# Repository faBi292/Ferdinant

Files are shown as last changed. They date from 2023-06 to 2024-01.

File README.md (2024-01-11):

# Ferdinant©️

---

## **IDLE Screens**

Es gibt 4 Anzeigen die mit den A,B,C und D ausgewählt werden können.

### **IDLE A**

<pre><code>Uhrzeit: hh:mm:ss
Tag: XX   LH:hh,h
</code></pre>

- "Uhrzeit", zeigt die interne Uhrzeit der Steuerung.
- "Tag", zeigt den aktuellen Tag des Modi, startet bei Tag 1.
- "LH", steht für Light Hours und gibt an wie viele Stunden Licht an diesem Tag schon vergangen sind.

### **IDLE B**

<pre><code>Rising: hh:mm:ss
Dawn  : hh:mm:ss
</code></pre>

- "Rising", gibt an wann das nächste mal das Licht angeschaltet wird.
- "Dawn", gibt an wann das Licht das nächste mal ausgeschaltet wird.

### **IDLE C**

<pre><code>Cycle: "MODE"
"MODE NAME"   "Days"
</code></pre>

- "MODE", gibt an welcher Modus gerade aktiv ist. (2002, 2004, 2006)
- "Mode Name", gibt den Namen des aktuellen Modus zurück (Half_Season, Full_season, Tropical)
- "Days", gibt an wie viele Tage der Modi benötigt.

### **IDLE D**

<pre><code>Glow: "%"

</code></pre>

- "Glow", gibt an wie groß die Lichtintensität des Lichtsensor ist.
- ℹ️ Das Licht gilt als an bei über 80% und als aus bei 30%, dazwischen ist eine Grauzone/Puffer und wechselt erst wenn die Schwelle über/unterschritten wurde.

---

## **LED's**

| Farbe | Bedeutung |
| --- | --- |
| 🔵 Blau | Leuchtet wenn Steckdose "An" sein soll und ist aus wenn Steckdose "Aus" sein soll. |
| 🟡 Gelb | Leuchtet auf wenn gefunkt wird. |
| 🔴 Rot  | Leuchtet wenn Fehler erkannt wird, unzwar wenn Lichtsensor nicht mit dem internen Wert übereinstimmt. |

---

## **Modus Auswahl**

Da zwischen 3 Modis unterschieden werden muss, ist wichtig zu verstehen wie man den Modi richtig einstellt.

Nach dreimaligen druecken der Sternchen Taste   `"*"`  auf dem Keypad, fragt das System, ob es einen Reset durch fuehren soll. Welches mit `"#"` bestaetigt werden kann, mit dem Druck einer anderen Taste wird das Menue automatischen wieder verlassen.

<pre><code>RESET MENU!
USE '#' 4 RESE
</code></pre>

Beachte, dass es moeglich ist zu jedem Zeitpunkt des Resetsablaufes, dass System kurz vom auszuschalten um den Vorgang zu unterbrechen. Dadurch wird einfach der Zustand vor dem Modi Auswahl beibehalten.

⚠️ Beachtet werden muss, dass während man in der Auswahl ist, dass System nicht die Steckdose steuern kann.

### **Jahr einstellen**

Wird der Reset bestaetigt oeffnet sich, das Menue das fragt welcher Modi ausgewaehlt werden soll. Dazu muss ein 4-stelliger Code eingegebn werden.Es tritt ein Fehler auf, wenn ein Code eingegben wird den das System nicht kennt. Danach wird man erneut angewiesen einen Code einzugeben.

**Dynamische Zyklen**

| Modi-Code | Modi-Name | Dauer |
| --- | --- | --- |
| 2000 | Half Season | 80 Tage  |
| 2001 | Full Season | 120 Tage |
| 2002 | Tropical | 100 Tage |

**Statische Zyklen**

| Modi-Code | Modi-Name | Lichtstunden pro Tag | Zeiten |
| --- | --- | --- | --- |
| 2003 | Veggie | 18h | 05:00 - 23:00 |
| 2004 | Production | 12h | 08:00 - 20:00 |
| 2005 | Short Veggie | 16h | 06:00 - 22:00 |

### **Setzen der Uhrzeit**

Ist der Code eingegebn wird nun nach der Uhrzeit (Stunde und Minute) gefragt. Hier empfielt es sich die aktuelle Uhrzeit zu benutzen um die Steuerung der Tageszeit anzupassen. Natuerlich ist eine andere Uhrzeit auch moeglich.
(Beachte: bei der Eingabe einer einstelligen Zahl wird folgende Formatierung erwartet Bsp.: fuer 6 Uhr muesste **'06'** eingegeben werden, das selbe gilt fuer die Minuten).

<pre><code>Stunde eingeben
Bsp. '13'
</code></pre>

### Setzen des Tages

Nun kann eingestellt werden wie viele, Tage übersprugnen werden sollen.

<pre><code>Tage skippen
Bsp. '023'
</code></pre>

Bsp. um am Tag 8 anzufangen muss die Zahl **'007'** eingegeben werden.

---

# **Schaltzyklen**

- ℹ️ Sobald ein **dynamischer** Zyklus über sein Ende hinaus verwendet wird, setzt er fortlaufend seine letzten Schaltzeiten ein.

**Statische Zyklen**

| Modi-Code | Modi-Name | Lichtstunden pro Tag | Zeiten |
| --- | --- | --- | --- |
| 2003 | Veggie | 18h | 05:00 - 23:00 |
| 2004 | Production | 12h | 08:00 - 20:00 |
| 2005 | Short Veggie | 16h | 06:00 - 22:00 |



---

# **Schaltplan**

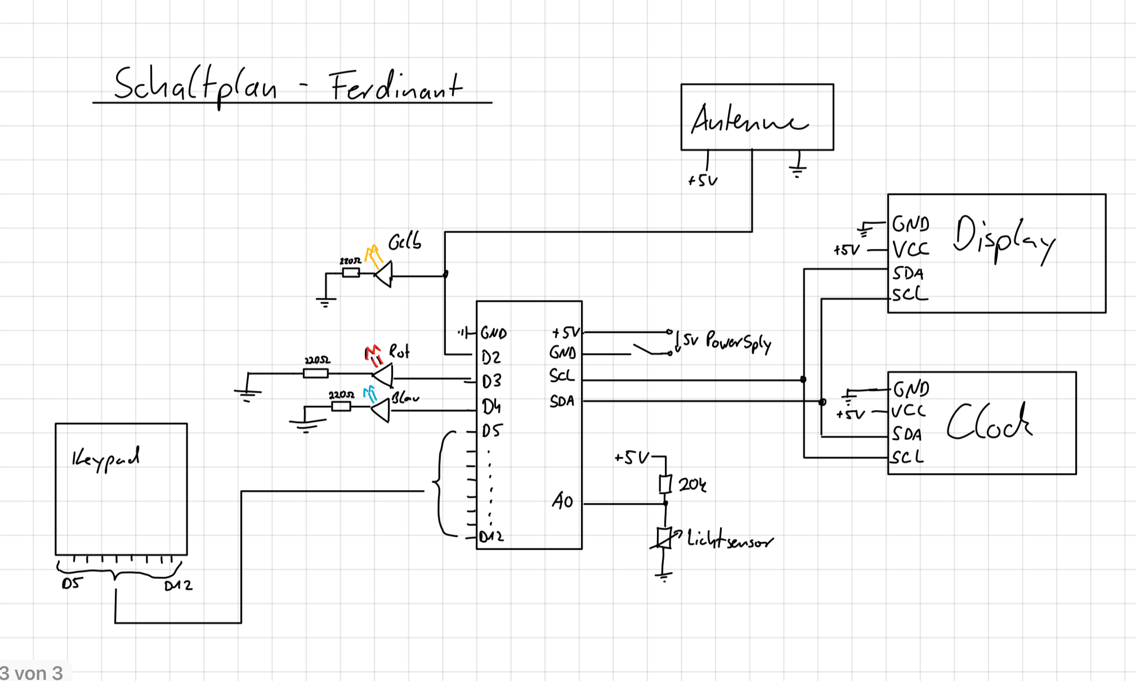
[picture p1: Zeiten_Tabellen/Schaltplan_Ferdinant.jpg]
Schaltplan


# **Code spezifische Notizen**

**Tri-State Codes**

<pre><code>AN = mySwitch.sendTriState("00000FFF0F0F");
</code></pre>

<pre><code>AUS = mySwitch.sendTriState("00000FFF0FF0");
</code></pre>

# Bauteile

| Komponente | Modell/Bezeichnung |
| --- | --- |
| Steckdose  | RCS 1000 N Comfort (Mx. 1000 Watt) |
| Uhr | RTC_DS3231 |
| Sender | 433_MHz Transmitter |
| Board | 16Mhz NANO V 3,0 Atmega328 |
| Display | LCD1602 |
| Keypad | 4x4 Matrix Tastatur |

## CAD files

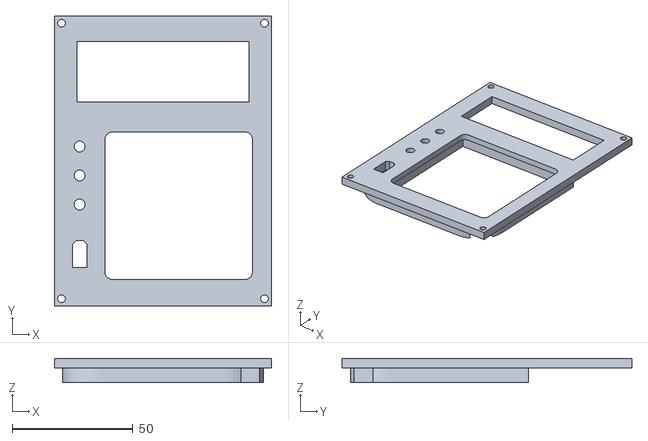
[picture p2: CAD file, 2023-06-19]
CAD_Modell/Ferdinant_Deckel_Sebi.stl
90.0 x 120.0 x 10.0

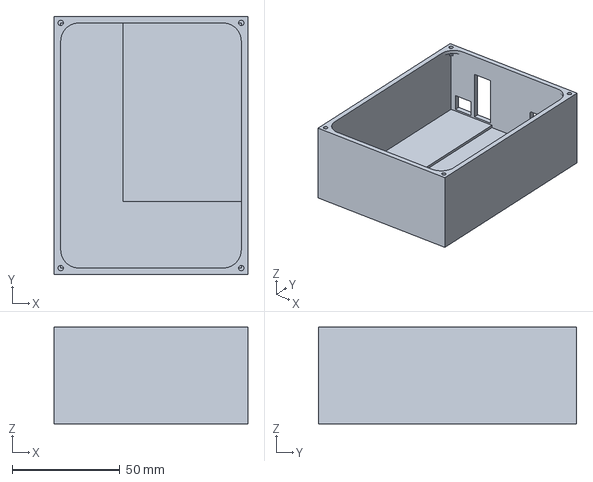
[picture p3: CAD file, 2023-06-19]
CAD_Modell/Ferdinant_Basis v2.3mf
90.0 x 120.0 x 45.0 mm

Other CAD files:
CAD_Modell/Ferdinant_Deckel_2.0 v2.3mf
CAD_Modell/Ferdinant_Basis_Sebi.stl
CAD_Modell/Ferdinant_Basis.stl
CAD_Modell/Ferdinant_Deckel.stl
CAD_Modell/Ferdinant_Basis v1.f3d
CAD_Modell/Ferdinant_Deckel v1.f3d

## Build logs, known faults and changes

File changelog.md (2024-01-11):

# CHANGELOG.md

## v1.3 (11.02.2024)

* 3 Neue Modi hinzugefügt (Veggie, Production, Short Veggie)

## v1.2 (01.05.2023)

- Offical Release

## v1.1-beta (01-05-2023)

- Modi's Angepasst 2002,2004,2006,
- I2C LCD Funktionen erweitert: ( Idle A,B,C und Energiespar Modus)
- Auf Nano Board umgestiegen
- Steckdose wird jetzt über Tri-State angestuert
- Implementierung des Lichtsensors

## v1.0-beta (26-03-2023)

- RC Modul funktionsfähig eingebunden
- Keypad Funktionen implementiert
- LCD Display integriert, 4 Idle-Modi, gute Ansteuerbarkeit der Knöpfe
- Reset Möglichkeit
- Bis jetzt nur ein Modi "2002"
- Kleine Test Led angebaut

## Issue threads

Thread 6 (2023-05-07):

im reset menu waitForKey() durch andere Loesung ersetzen um Sicherheit zu erhoehen

faBi292, 2023-05-07:

faBi292, 2023-10-01:
Es wurde in der readme auf das Problem hingewiesen und sollte leicht zu vermeiden sein.

Closed 2023-10-01.

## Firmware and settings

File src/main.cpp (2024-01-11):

#include <Arduino.h>
#include <Keypad.h>
#include <RTClib.h>
#include <SPI.h>
#include <Wire.h>
#include <LiquidCrystal_I2C.h>
#include <RCSwitch.h>

#define Red_LED_PIN 2
#define Blue_LED_PIN 3
#define RC_PIN 4

RTC_DS3231 rtc;
RCSwitch mySwitch;

const int HALF_SEASON = 2000;
const int FULL_SEASON = 2001;
const int TROPICAL = 2002;
const int VEGGIE = 2003;
const int PRODUCTION = 2004;
const int SHORT_VEGGIE = 2005;

const byte ROWS = 4; // four rows
const byte COLS = 4; // four columns

// Map the buttons to an array for the Keymap instance
char hexaKeys[ROWS][COLS] = {
    {'1', '2', '3', 'A'},
    {'4', '5', '6', 'B'},
    {'7', '8', '9', 'C'},
    {'*', '0', '#', 'D'}};

byte colPins[ROWS] = {5, 6, 7, 8};    // Pins used for the rows of the keypad
byte rowPins[COLS] = {9, 10, 11, 12}; // Pins used for the columns of the keypad

// Initialise the Keypad
Keypad customKeypad = Keypad(makeKeymap(hexaKeys), rowPins, colPins, ROWS, COLS);

typedef struct
{
  uint16_t jahr = 2008;
  uint8_t stunde = 13;
  uint8_t minute = 17;
  uint8_t sekunde = 8;
  uint16_t tag = 1;

} time_struct;

// const int rs = A0, en = A1, d4 = A2, d5 = A3, d6 = 10, d7 = 11;
// LiquidCrystal lcd(rs, en, d4, d5, d6, d7);
LiquidCrystal_I2C lcd(0x27, 16, 2); // I2C address, number of columns and rows

enum zustaende
{
  Knopf_A,
  Knopf_B,
  Knopf_C,
  Knopf_D,
};

int LICHT_CHECK_intern; // Sagt aus ob Licht an sein muss
int LICHT_CHECK_extern; // Sagt aus ob Licht gerade an ist via. Photosensor
unsigned days_passed;   // Vergangene Tage beginnend bei 1
char getKey_puffer;     // zuletzt eingegebene Taste wird hier gespeichert

void set_usertime();                                            // Erm├╢glicht den Benutzer seine Einstellung vorzunehmen.
void print_time();                                              // Printed die aktuelle Uhrzeit der Uhr
void print_time_passed();                                       // Printed die verstrichene Zeit seit anfang der Einstellung.
unsigned int get_days_passed();                                 // Berechnet die verstrichenen Tage seit anfang der Einstellung.
uint32_t get_seconds_passed_daily();                            // Berechnet die verstrichenen Sekunden seit 0 Uhr.
int check_status(uint32_t aufgang_sek, uint32_t untergang_sek); // gibt 1 f├╝r Licht muss an sein und 0 f├╝r Licht muss aus sein.
uint32_t get_offset();                                          // Berechnet den Offset in bezug zu 1970 zu dem jeweiligen start datum der einstellung. Bsp sekunden von 1970 bis 2002
void increaseDateTime(DateTime &dt, int days);                  // Erh├╢ht das Datum einer DateTime Variablen um eine Anzahl von Tagen
void check_star();                                              // ├£berpr├╝ft ob die Sternchentaste gedr├╝ckt geahlten wird, nach 3 Sekunden f├╝hrt sie dann set_usertime() aus.
uint32_t check_aufgang_sek(unsigned int days);                  // Bekommt die vergangen Tage ├╝bergeben und gibt die Aufgangsuhrzeit zur├╝ck
uint32_t check_untergang_sek(unsigned int days);                // Bekommt die vergangen Tage ├╝bergeben und gibt die Untergangsuhrzeit zur├╝ck
void display_idle(char Knopf);                                  // Bekommt A,B,C,D ├╝bergebn und wechselt dann in den entsprechenden Modi
void check_Knopf();                                             // ├£berpr├╝ft ob Knopf gedr├╝ckt wurde und ruft entsprechend die Funktion auf
void secondsToTime(uint32_t seconds, char *timeString);         // Bekommt Sekunden als eingabe Wert und gibt sie ahls "HH:MM" format aus
void secondsToFullTime(uint32_t seconds, char *timeString);     // Bekommt Sekunden als eingabe Wert und gibt sie ahls "HH:MM:SS" format aus
void secondsToHour(uint32_t seconds, char *timeString);         // Bekommt Sekunden als eingabe Wert und gibt sie ahls "HH,H" format aus
float read_LichtSensor();                                       // Gibt die Aktuelle Lichtintensität in % zurück
uint32_t get_lightseconds();                                    // Gibt die Sekunden die an dem Tag schon das Lich an ist wieder

void init_RCSwitch(int PIN, int PulseLength);
void steckdose_on(int state); // Kann Steckdose ein und ausschalten 1:EIN / 0:AUS

void lcd_energiesparen(int timer_reset); // Steuert die Hitnergrundbeleuchtung
int licht_check_photosensor();

// void transmit_data(int state);

void setup()
{
  Serial.begin(9600); // Initialise the serial monitor

  lcd.init();
  lcd_energiesparen(1);

  lcd.print("Loading");
  delay(300);
  lcd.print(".");
  delay(300);
  lcd.print(".");
  delay(300);
  lcd.print(".");
  delay(300);

  Wire.begin();
  rtc.begin();

  init_RCSwitch(RC_PIN, 324);

  if (!rtc.begin())
  {
    lcd.clear();
    lcd.println("RTC not found!");
    while (1)
      ;
  }

  pinMode(Red_LED_PIN, OUTPUT);  // Rote LED
  pinMode(Blue_LED_PIN, OUTPUT); // Blaue LED

  pinMode(A0, INPUT); // Licht_Sensor

  /*digitalWrite(Red_LED_PIN, HIGH);
  for (int i = 1; i < 121; i++)
  {
    Serial.println((String)i + ":" + check_aufgang_sek(i) + ":" + check_untergang_sek(i));
  }*/
  // DateTime dt1(2006, 1, 1, 0, 0, 0); //Findet den Offset raus
  // Serial.println(dt1.unixtime());
}

void loop()
{
  static unsigned long lastTime_1000 = 0;
  static unsigned long lastTime_30000 = 0;

  check_Knopf();

  if (millis() - lastTime_1000 >= 1000)
  {

    lastTime_1000 = millis(); // setzt Schleife zur├╝ck

    days_passed = get_days_passed();

    LICHT_CHECK_intern = check_status(check_aufgang_sek(days_passed), check_untergang_sek(days_passed)); // 6.5ms
    analogWrite(Blue_LED_PIN, LICHT_CHECK_intern * 30);
    LICHT_CHECK_extern = licht_check_photosensor();

    static boolean status = !LICHT_CHECK_intern; // Gibt an ob die Initialsendung nach Switch schon erfolgt ist
    if (status != LICHT_CHECK_intern)
    {
      status = LICHT_CHECK_intern;
      steckdose_on(LICHT_CHECK_intern);
    }

    if (LICHT_CHECK_extern != LICHT_CHECK_intern)
    {
      digitalWrite(Red_LED_PIN, HIGH);
      steckdose_on(LICHT_CHECK_intern);
    }
    else
    {
      digitalWrite(Red_LED_PIN, LOW);
    }

    lcd_energiesparen(0); // Aktualisiert die energiespar Funktion

    display_idle(' '); // 9ms
  }

  if (millis() - lastTime_30000 >= 30000) // Setzt alle 30 Sekunden Signal raus
  {
    lastTime_30000 = millis(); // setzt Schleife zur├╝ck

    if (LICHT_CHECK_intern)
    {
      steckdose_on(1);
    }
    else
    {
      steckdose_on(0);
    }
  }
}

void check_Knopf()
{
  getKey_puffer = customKeypad.getKey();

  if (getKey_puffer)
  {
    lcd_energiesparen(1);
  }
  if (getKey_puffer == 'A')
  {
    display_idle('A');
  }
  else if (getKey_puffer == 'B')
  {
    display_idle('B');
  }
  else if (getKey_puffer == 'C')
  {
    display_idle('C');
  }
  else if (getKey_puffer == 'D')
  {
    display_idle('D');
  }
  else if (getKey_puffer == '*')
  {
    check_star();
  }
  else if (getKey_puffer == '0')
  {
    steckdose_on(0);
  }
  else if (getKey_puffer == '1')
  {
    steckdose_on(1);
  }
}

void display_idle(char Knopf)
{
  static DateTime now;
  static zustaende idle_zustand = Knopf_A;
  static char puffer = Knopf_A;
  static char time_puffer[10];

  if (Knopf != ' ')
  {
    puffer = Knopf;
  }

  if (puffer == 'A')
  {
    idle_zustand = Knopf_A;
  }
  else if (puffer == 'B')
  {
    idle_zustand = Knopf_B;
  }
  else if (puffer == 'C')
  {
    idle_zustand = Knopf_C;
  }
  else if (puffer == 'D')
  {
    idle_zustand = Knopf_D;
  }

  switch (idle_zustand)
  {
  case Knopf_A:

    secondsToFullTime(get_seconds_passed_daily(), time_puffer);
    lcd.setCursor(0, 0);
    lcd.print((String) "Uhrzeit:" + time_puffer + "    ");
    lcd.setCursor(0, 1);
    lcd.print((String) "Tag:" + get_days_passed() + "   ");
    lcd.setCursor(8, 1);
    secondsToHour(get_lightseconds(), time_puffer);
    lcd.print((String) "LH:" + time_puffer + "h        ");
    break;

  case Knopf_B:

    secondsToFullTime(check_aufgang_sek(get_days_passed()), time_puffer);
    lcd.setCursor(0, 0);
    lcd.print((String) "Rising: " + time_puffer + "   ");
    secondsToFullTime(check_untergang_sek(get_days_passed()), time_puffer);
    lcd.setCursor(0, 1);
    lcd.print((String) "Dawn  : " + time_puffer + "   ");
    break;

  case Knopf_C:

    now = rtc.now();

    lcd.setCursor(0, 0);
    lcd.print((String) "Cycle: " + now.year() + "      ");
    lcd.setCursor(0, 1);
    if (now.year() == HALF_SEASON)
    {
      lcd.print("Half Season  80d  ");
    }
    else if (now.year() == FULL_SEASON)
    {
      lcd.print("Full Season 120d ");
    }
    else if (now.year() == TROPICAL)
    {
      lcd.print("Tropical    100d ");
    }
    else if (now.year() == VEGGIE)
    {
      lcd.print("Veggie       18h ");
    }
    else if (now.year() == PRODUCTION)
    {
      lcd.print("Production   12h ");
    }
    else if (now.year() == SHORT_VEGGIE)
    {
      lcd.print("Short Veg.   16h ");
    }
    else
    {
      lcd.print("NO MODE          ");
    }

    break;

  case Knopf_D:

    static float brightness_precent;

    brightness_precent = read_LichtSensor();

    lcd.setCursor(0, 0);
    lcd.print((String) "Glow: " + brightness_precent + "%           ");
    lcd.setCursor(0, 1);

    lcd.print((String) "                         ");

    break;
  }
}

void check_star()
{
  static uint8_t counter = 0;
  static unsigned long lasttime = 0;

  // Serial.println(millis() - lasttime);

  if (millis() - lasttime >= 1000)
  {
    counter = 0;
    lasttime = millis();
  }

  if (getKey_puffer == '*')
  {
    counter++;
    lasttime = millis();
  }

  if (counter > 2)
  {
    lcd.clear();
    lcd.setCursor(0, 0);
    lcd.print("RESET MENU!");
    lcd.setCursor(0, 1);
    lcd.print("USE '#' 4 RESET");

    if (customKeypad.waitForKey() == '#') // hier m∩┐╜sste eigentlich eine bessere L∩┐╜sung her
    {
      set_usertime();
      counter = 0;
    }
    else
    {
      counter = 0;
    }
  }
}

void set_usertime()
{
  int set_process = 0;   // Zaehler Variable
  time_struct user_time; // Defeniert neuen Zeit Speicher

  // erste Schleife f├╝r Jahr / Code
  do
  {
    lcd.clear();
    lcd.setCursor(0, 0);
    lcd.print("Modi eingeben");
    lcd.setCursor(0, 1);
    lcd.print("Bsp.'2008' ");

    char user_time_code[5] = "2008";

    for (int i = 0; i < 4; i++)
    {
      user_time_code[i] = customKeypad.waitForKey();
      lcd.print(user_time_code[i]);
    }
    delay(400);
    lcd.clear();
    lcd.print("Eingabe: ");
    lcd.print(user_time_code[0]);
    lcd.print(user_time_code[1]);
    lcd.print(user_time_code[2]);
    lcd.print(user_time_code[3]);
    // Serial.println(String("Eingabe: ") + user_time_code[0] + user_time_code[1] + user_time_code[2] + user_time_code[3]);

    if (atoi(user_time_code) == HALF_SEASON)
    {
      set_process = 1;
      user_time.jahr = atoi(user_time_code);
      lcd.setCursor(0, 1);
      lcd.print("HALF SEASON");
      delay(2000);
    }
    else if (atoi(user_time_code) == FULL_SEASON)
    {
      set_process = 1;
      user_time.jahr = atoi(user_time_code);
      lcd.setCursor(0, 1);
      lcd.print("FULL SEASON");
      delay(2000);
    }
    else if (atoi(user_time_code) == TROPICAL)
    {
      set_process = 1;
      user_time.jahr = atoi(user_time_code);
      lcd.setCursor(0, 1);
      lcd.print("TROPICAL");
      delay(2000);
    }
    else if (atoi(user_time_code) == VEGGIE)
    {
      set_process = 1;
      user_time.jahr = atoi(user_time_code);
      lcd.setCursor(0, 1);
      lcd.print("VEGGIE");
      delay(2000);
    }
    else if (atoi(user_time_code) == PRODUCTION)
    {
      set_process = 1;
      user_time.jahr = atoi(user_time_code);
      lcd.setCursor(0, 1);
      lcd.print("PRODUCTION");
      delay(2000);
    }
    else if (atoi(user_time_code) == SHORT_VEGGIE)
    {
      set_process = 1;
      user_time.jahr = atoi(user_time_code);
      lcd.setCursor(0, 1);
      lcd.print("SHORT_VEGGIE");
      delay(2000);
    }
    else
    {
      lcd.clear();
      lcd.print("NOT FOUND!");
      delay(600);
    }

  } while (set_process == 0);

  // zweite Schleife f├╝r Stunde
  do
  {
    lcd.clear();
    lcd.setCursor(0, 0);
    lcd.print("Stunde eingeben");
    lcd.setCursor(0, 1);
    lcd.print("Bsp.'13' ");

    char user_time_code[3] = "13";

    for (int i = 0; i < 2; i++)
    {
      user_time_code[i] = customKeypad.waitForKey();
      lcd.print(user_time_code[i]);
    }
    delay(400);
    lcd.clear();
    lcd.print("Eingabe: ");
    lcd.print(user_time_code[0]);
    lcd.print(user_time_code[1]);
    lcd.print(" Uhr!");
    delay(1000);

    if (atoi(user_time_code) < 24)
    {
      set_process = 2;
      user_time.stunde = atoi(user_time_code);
    }
    else
    {
      lcd.clear();
      lcd.print("UHRZEIT ZU GROSS");
      delay(600);
    }

  } while (set_process == 1);

  // dritte Schleife f├╝r Minuten
  do
  {
    lcd.clear();
    lcd.print("Minuten Eingeben");
    lcd.setCursor(0, 1);
    lcd.print("Bsp.'41' ");

    char user_time_code[3] = "41";

    for (int i = 0; i < 2; i++)
    {
      user_time_code[i] = customKeypad.waitForKey();
      lcd.print(user_time_code[i]);
    }

    delay(400);

    lcd.clear();
    lcd.print("Eingabe: ");
    lcd.print(user_time_code[0]);
    lcd.print(user_time_code[1]);
    lcd.print(" min!");

    delay(1000);

    if (atoi(user_time_code) < 60)
    {
      set_process = 3;
      user_time.minute = atoi(user_time_code);
    }
    else
    {
      lcd.clear();
      lcd.print("UHRZEIT ZU GROSS");
      delay(600);
    }

  } while (set_process == 2);

  // vierte Schleife f├╝r Tage
  do
  {
    lcd.clear();
    lcd.setCursor(0, 0);
    lcd.print("Tage skippen");
    lcd.setCursor(0, 1);
    lcd.print("Bsp.'023' ");

    char user_time_code[4] = "023";

    for (int i = 0; i < 3; i++)
    {
      user_time_code[i] = customKeypad.waitForKey();
      lcd.print(user_time_code[i]);
    }

    delay(400);
    lcd.clear();
    lcd.print("Eingabe: ");
    lcd.print(user_time_code[0]);
    lcd.print(user_time_code[1]);
    lcd.print(user_time_code[2]);
    delay(1000);

    if (atoi(user_time_code) < 300)
    {
      set_process = 4;

      rtc.adjust(DateTime(user_time.jahr, 1, 1, user_time.stunde, user_time.minute, 30) + TimeSpan(atoi(user_time_code), 0, 0, 0));
    }
    else
    {
      lcd.clear();
      lcd.println("TAGE ZU GROSS");
      delay(600);
    }

  } while (set_process == 3);

  lcd_energiesparen(1);
  lcd.clear();
  lcd.print("SUCCESS");
  lcd.setCursor(0, 1);
  lcd.print("Loading...");

  delay(2000);
}

void print_time()
{

  DateTime now = rtc.now();

  Serial.print(now.year(), DEC);
  Serial.print('/');
  Serial.print(now.month(), DEC);
  Serial.print('/');
  Serial.print(now.day(), DEC);
  Serial.print(' ');
  Serial.print(now.hour(), DEC);
  Serial.print(':');
  Serial.print(now.minute(), DEC);
  Serial.print(':');
  Serial.print(now.second(), DEC);
  Serial.println();
}

void print_time_passed()
{
  static DateTime now;
  static uint32_t sekunden_offset;

  now = rtc.now();

  sekunden_offset = get_offset();

  Serial.println(now.unixtime() - sekunden_offset);
}

uint32_t get_seconds_passed_daily()
{
  static DateTime now;
  static uint32_t sekunden_passed_day;

  now = rtc.now();

  sekunden_passed_day = (now.unixtime() - get_offset()) % (86400); // 86400 = 60*60*24

  return sekunden_passed_day;
}

int check_status(uint32_t aufgang_sek, uint32_t untergang_sek)
{
  if ((get_seconds_passed_daily() > aufgang_sek))
  {
    if ((get_seconds_passed_daily() < untergang_sek))
    {
      return 1;
    }
    else
    {
      return 0;
    }
  }
  else
  {
    return 0;
  }
}

uint32_t get_offset()
{ //TODO Check if Offsets are correct
  static DateTime now;

  now = rtc.now();

  if (now.year() == HALF_SEASON)
  {
    return 946684800;
  }
  if (now.year() == FULL_SEASON)
  {
    return 978307200;
  }
  if (now.year() == TROPICAL)
  {
    return 1009843200;
  }
  if (now.year() == VEGGIE)
  {
    return 1041379200;
  }
  if (now.year() == PRODUCTION)
  {
    return 1072915200;
  }
  if (now.year() == SHORT_VEGGIE)
  {
    return 1104537600;
  }

  return 0; // Falls es das Jahr nicht mehr geben sollte, k├╢nnte passieren wenn die Uhr lange nicht benutzt wird.
}

unsigned int get_days_passed()
{

  static DateTime now;
  static uint32_t puffer;
  static unsigned int counter;

  counter = 1;
  now = rtc.now();

  puffer = now.unixtime() - get_offset();

  while (puffer >= 86400)
  {
    puffer = puffer - 86400;
    counter++;
  }

  return counter;
}

void increaseDateTime(DateTime &dt, int days)
{
  dt = dt + TimeSpan(days, 0, 0, 0);
}

uint32_t check_aufgang_sek(unsigned int days)
{
  static DateTime now;

  now = rtc.now();

  if (now.year() == HALF_SEASON)
  {
    if (days > 80)
    {
      return (uint32_t)(27000);
    }
    return (uint32_t)(21600 + (5400 / 79.0) * (days - 1)); // Von 6:00 -> 7:30
  }

  if (now.year() == FULL_SEASON)
  {
    if (days > 120)
    {
      return (uint32_t)(27000);
    }
    return (uint32_t)(18000 + (9000 / 119.0) * (days - 1)); // Von 5:00 -> 7:30
  }

  if (now.year() == TROPICAL) 
  {
    if (days <= 10)
    {
      return (uint32_t)(21600);
    }
    else if (days <= 20)
    {
      return (uint32_t)(21600 + (1800 / 10) * (days - 10));
    }
    else if (days <= 40)
    {
      return (uint32_t)(23400 + (1800 / 20) * (days - 20));
    }
    else if (days <= 80)
    {
      return (uint32_t)(25200);
    }
    else if (days <= 100)
    {
      return (uint32_t)(25200 + (1800 / 20) * (days - 80));
    }
    else if (days > 100)
    {
      return (uint32_t)(27000);
    }
  }

  if (now.year() == VEGGIE)
  {
    return (uint32_t)(18000); // 5:00 Uhr
  }

  if (now.year() == PRODUCTION)
  {
    return (uint32_t)(28800); // 8:00 Uhr
  }

  if (now.year() == SHORT_VEGGIE)
  {
    return (uint32_t)(21600); // 6:00 Uhr
  }

  return 0;

}

uint32_t check_untergang_sek(unsigned int days)
{
  static DateTime now;

  now = rtc.now();

  if (now.year() == HALF_SEASON)
  {
    if (days > 80)
    {
      return (uint32_t)(66600);
    }
    return (uint32_t)(72000 - (5400 / 79.0) * (days - 1)); // Von 20:00 -> 18:30
  }

  if (now.year() == FULL_SEASON)
  {
    if (days > 120)
    {
      return (uint32_t)(66600);
    }
    return (uint32_t)(75600 - (9000 / 119.0) * (days - 1)); // Von 21:00 -> 18:30
  }

  if (now.year() == TROPICAL)
  {
    if (days <= 10)
    {
      return (uint32_t)(68400);
    }
    else if (days <= 20)
    {
      return (uint32_t)(68400 - (1800 / 10) * (days - 10));
    }
    else if (days <= 40)
    {
      return (uint32_t)(66600 - (1800 / 20) * (days - 20));
    }
    else if (days <= 80)
    {
      return (uint32_t)(64800);
    }
    else if (days <= 100)
    {
      return (uint32_t)(64800 - (1800 / 20) * (days - 80));
    }
    else if (days > 100)
    {
      return (uint32_t)(63000);
    }
  }

  if (now.year() == VEGGIE)
  {
    return (uint32_t)(82800); // 23:00 Uhr
  }

  if (now.year() == PRODUCTION)
  {
    return (uint32_t)(72000); // 20:00 Uhr
  }

  if (now.year() == SHORT_VEGGIE)
  {
    return (uint32_t)(79200); // 22:00 Uhr
  }

  return 0;
}

void secondsToTime(uint32_t seconds, char *timeString)
{
  int hours = seconds / 3600;
  int minutes = (seconds % 3600) / 60;
  sprintf(timeString, "%02d:%02d", hours, minutes);
}

void secondsToFullTime(uint32_t seconds, char *timeString)
{
  int hours = seconds / 3600;
  int minutes = (seconds % 3600) / 60;
  int sec = seconds % 60;
  sprintf(timeString, "%02d:%02d:%02d", hours, minutes, sec);
}

void secondsToHour(uint32_t seconds, char *timeString)
{
  float hours = (float)seconds / 3600.0;
  int wholeHours = (int)hours;
  int decimalHours = (int)(hours * 10) % 10;
  sprintf(timeString, "%02d.%01d", wholeHours, decimalHours);
}

uint32_t get_lightseconds()
{
  static uint32_t days;

  days = get_days_passed();

  if (get_seconds_passed_daily() > check_aufgang_sek(days))
  {
    if (get_seconds_passed_daily() < check_untergang_sek(days))
    {
      return (get_seconds_passed_daily() - check_aufgang_sek(days)); // Wenn noch TAG
    }
    else
    {
      return (check_untergang_sek(days) - check_aufgang_sek(days)); // Bei NACHT
    }
  }
  else
  {
    return 0; // AM Morgen
  }
}

/*void transmit_data(int state)
{
  if (state == 1)
  {
    mySwitch.send("000000000001010100010001"); // D AN
    mySwitch.send("000000000001010100010001");
    mySwitch.send("000000000001010100010001");
  }
  else if (state == 0)
  {
    mySwitch.send("000000000001010100010100"); // D AUS
    mySwitch.send("000000000001010100010100");
    mySwitch.send("000000000001010100010100");
  }
  return 0;

}*/

void init_RCSwitch(int PIN, int PulseLength)
{
  mySwitch = RCSwitch();
  mySwitch.enableTransmit(PIN);
  mySwitch.setPulseLength(PulseLength);
  // mySwitch.setProtocol(1);
}

void steckdose_on(int state)
{
  if (state == 1)
  { // Steckdose Einschalten
    mySwitch.sendTriState("00000FFF0F0F");
    // mySwitch.send(5393, 24);
  }
  else
  { // Steckdose Ausschalten
    mySwitch.sendTriState("00000FFF0FF0");
    // mySwitch.send(5396,24);
  }
}

void lcd_energiesparen(int timer_reset)
{
  static uint16_t last_millis = 0;
  static uint16_t delta = 0;

  if (timer_reset == 1)
  {
    last_millis = millis();
    lcd.backlight();
  }
  delta = millis() - last_millis;

  if (delta > 30000) // Macht nach 30 Sekunden wieder die Hintergrundbeleuchtung AUS
  {
    lcd.noBacklight();
  }
}
float read_LichtSensor()
{
  return map(analogRead(A0), 0, 1023, 100.0, 0.0);
}

int licht_check_photosensor()
{
  static float puffer;
  puffer = read_LichtSensor();
  if (puffer > 80)
  {
    return 1;
  }
  else if (puffer < 30)
  {
    return 0;
  }
}

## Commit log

2023-04-13 Implementierung der Funktionen 04 06
2023-04-23 Neue I2C LCD Implementiert
2023-05-01 Energiespar Modus hinzugefgt und triState Sendung
2023-05-03 Licht Sensor eingebaut
2023-05-03 Licht Sensor eingestellt und
2023-05-05 AN und AUS steuerbar mit 0 / 1
2023-06-19 Licht Sensor neue Funktion und ReadMe
    [Ferdinant_Basis v2.3mf, Ferdinant_Basis.stl, Ferdinant_Basis_Sebi.stl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]
2023-06-19 Readme + xlxc
    [Zeiten.xlsx]
